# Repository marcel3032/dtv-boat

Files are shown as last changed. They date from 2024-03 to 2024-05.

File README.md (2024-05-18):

# dtv-boat

Zdrojáky a súbory k návrhu loďky na diaľkové ovládanie na predmet Digitálne technológie výroby.

## Úvod a popis lode

Cieľom projektu je postaviť diaľkovo ovládanú loďku.
Loďka bude z dreva (preglejka/balza), ktoré bude rezané na laseri.
Lodná skrutka, kormidlo a konzola kormidla bude tlačené na 3D tlačiarni.
Elektronická časť modelu sa skladá z 2,4GHz pištoľovej vysielačky a prijímača.
Pohon modelu sa skladá z jednosmerného (brushed) 21 závitového (21T) motora typu 550.
Regulátor je 80A na 2-3 článkovú LiXX alebo 4-9 článkovú Ni-XX baterku.
Regulátor má vstavaný 5A BEC, ktorý ale má 7.4V/6.4V.
~~Keďže prijímač a servo je do 6V, tak ho možno budeme musieť regulovať na menšie napätie,
čo zrejme budeme robiť výkonovou diódou.~~ Edit: servo aj prijímač 6.4V napájanie zvládnu, takže nakoniec takéto nebolo potrebné.
Ovládanie kormidla zabezpečuje 3kg servo, ktoré je dvojicou bowdenov spojené s kormidlom.

Chladenie motoru a regulátoru je vodné. Voda je odoberaná za lodnou skrutkou na kormidle, odkiaľ je tlakom hnaná cez regulátor a následne motor.
Pre motor sme kúpili medený vodný chladič, pre regulátor bol vyrobený z tenkej medenej/hliníkovej trubky vloženej medzi rebrovanie chladiča.

Výkon je z motoru vedený kardanovým kĺbom priamo na hriadeľ s lodnou skrutkou bez prevodovky alebo redukcie.
Hriadeľ je cez dvojicu ložísk osadená v puzdre, ktoré je vlepené do trupu lode.

## Lodná skrutka

Lodná skrutka je navrhnutá v programe OpenSCAD. [Zdrojový kód](propeller/propeller.scad) je v repozitári.
List lodnej skutky má elipsový tvar a je prehnutý (`skew`). List má po celej svojej dĺžky rovnaký profil, mení sa iba jeho hĺbka.
Profil listu je zo 4 číslnej NACA série, pre našu loď bol pôvodne vybratý profil NACA 2412, t.j. prehnutý profil s 12% hrúbkou.
List je samozrejme pre zachovanie koštantného stúpania počas celej dĺžky skrútený
( $\alpha = atan2(S, 2 \pi r)$ , kde $S$ je stúpanie listu a $r$ je vzdialenosť osi otáčania).

Zrejme budeme počas vývoja experimentovať s rôznymi priemermi, stúpaniami skutky a profilmi.

*Profil NACA 2412:*

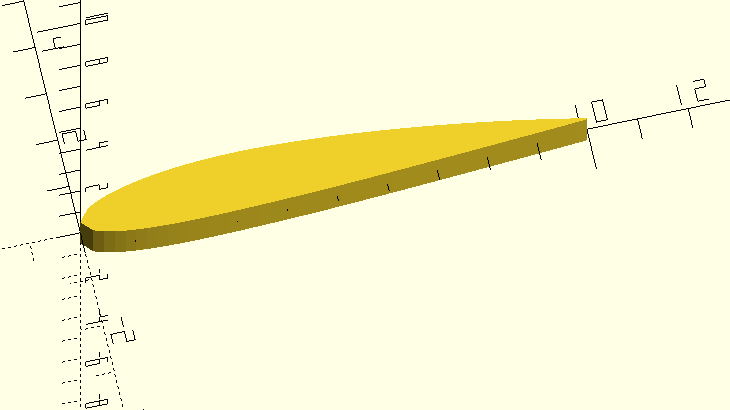
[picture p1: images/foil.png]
Profil NACA 2412


*Jeden list:*

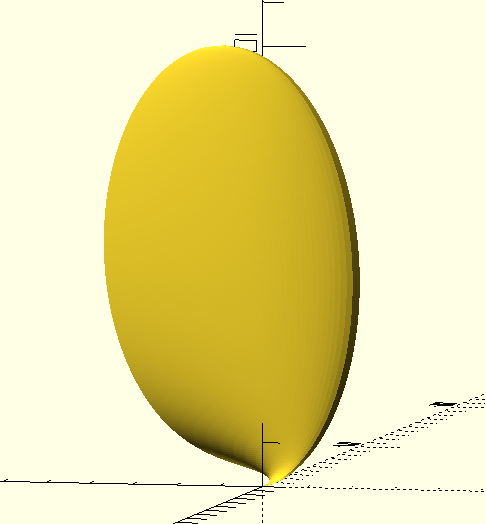
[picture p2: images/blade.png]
Jeden list


*Kompletná lodná skrutka aj s nábojom:*

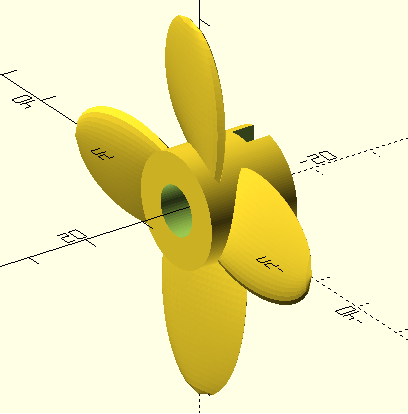
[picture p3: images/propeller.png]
Kompletná lodná skrutka aj s nábojom


## Trup lode

Trup lode je klasická drevená konštrukcia s preglejkovými priečkami a opláštením.
V trupe sa nachádzajú 4 priečne priečky (z toho posledné dve sú zdvojené) a 2 pozdĺžne.
Priečky rezané na laseri a sú z 3mm hrubej preglejky.

Opláštenie lode je z 1.5mm hrubej preglejky rezanej na laseri.

Trup lode je opäť navrhnutý v OpenSCADe a tvary priečok sú vyexportované priamo z tohoto programu.
[Zdrojový kód](boat.scad) je tiež v repozitári.

*Trup lode:*

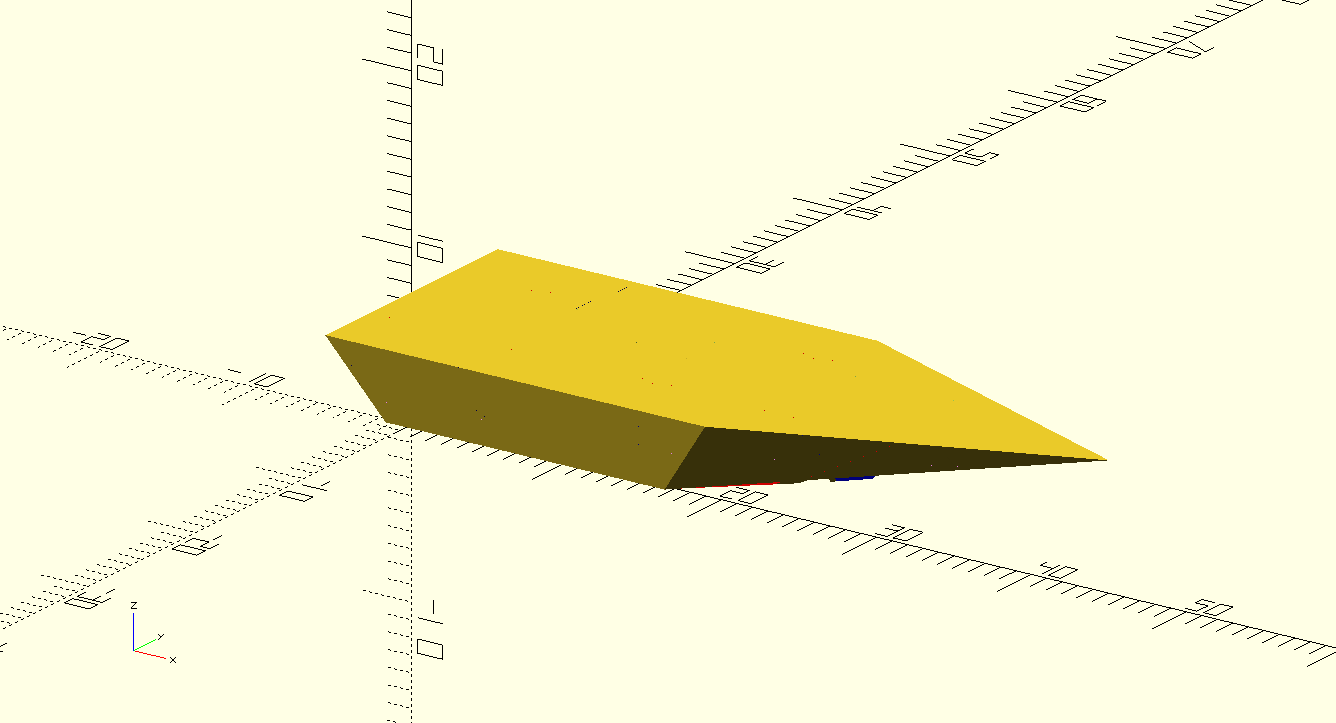
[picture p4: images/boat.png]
Trup lode


*Priečky v lodi:*

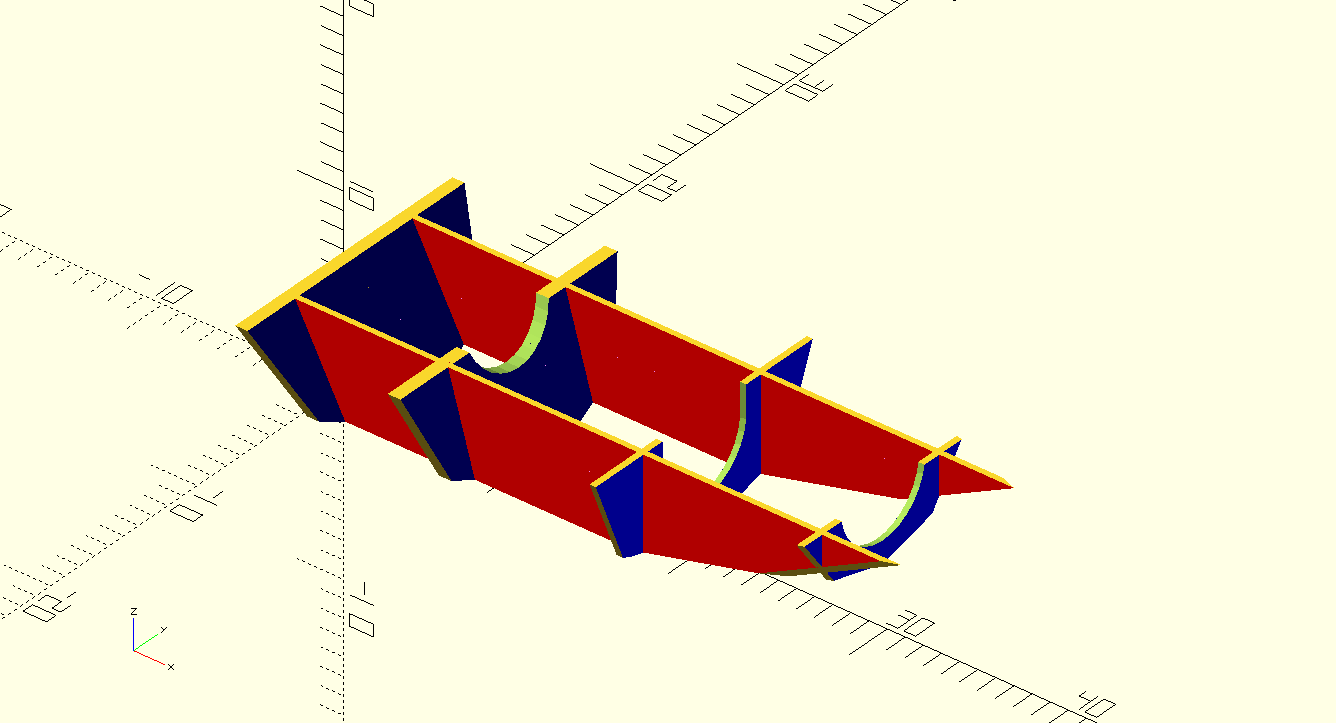
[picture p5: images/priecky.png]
Priečky v lodi


*Priečky pripravené na rezanie:*

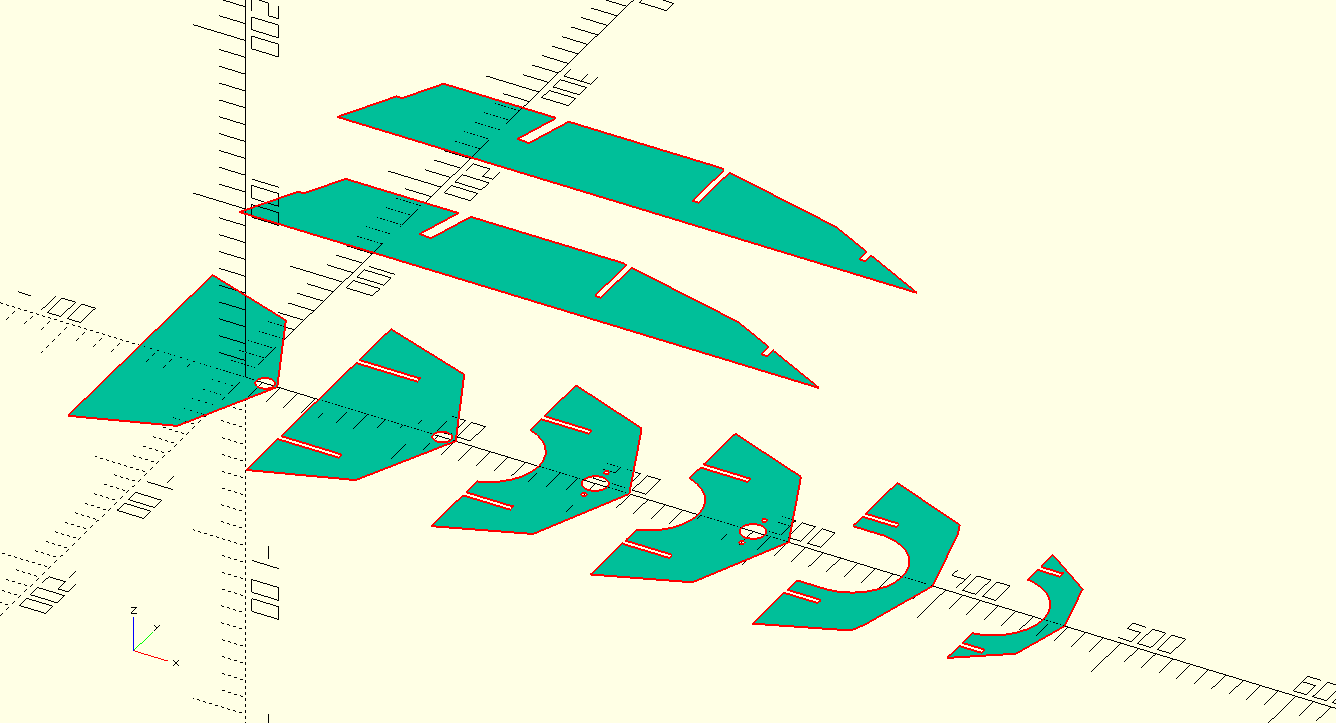
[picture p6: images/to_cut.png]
Priečky pripravené na rezanie


Opláštenie lode nie je priamo z OpenSCADu.
Namiesto toho sú z programu vyexportované súradnice vrcholov útvarov z ktorých sa opláštenie skladá.
Tieto útvary sú následne Python skriptom zrotované a sú vypočítané ich súradnice.
[Python skript](rotate_3d_polygons.py) je opäť v repozitári.

## Konzola kormidla a kormidlo

Konzola kormidla a kormmidlo boli navrhnuté v OpenSCADe a vytlačené na 3D tlačiarni.
Konzola má obdĺžnikový prierez a je k trupu lode cez plochú doštičku pripevnená štyrmi skrutkami M3.
Na konci konzoly je miesto na osku kormidla.
Oska je z nerezového drôtu priemeru 3.2mm a na vrchu je závlačkou pripevnená ku konzole.
Profil kormidla je rovnostranný trojuholník otočený základňou od smeru plavby.
Vo vnútri kormidla sa nachádza kanál na vstup chladiacej vody.
Vstup tohoto kanálu je otočený smerom k lodnej skrutke, aby tlačila vodu cez chladiaci kanál.
Z výstupu vodného kanála na vrchnej časti lode je voda odvádzaná umelohmotnou hadičkou ďalej do trupu lode.
Na vrchnej časti kormidla sa nachádzajú páky riadenia.

*Konzola kormidla aj s kormidlom (v zadnej časti kormidla je viditeľný kanál na chladiacu vodu):*

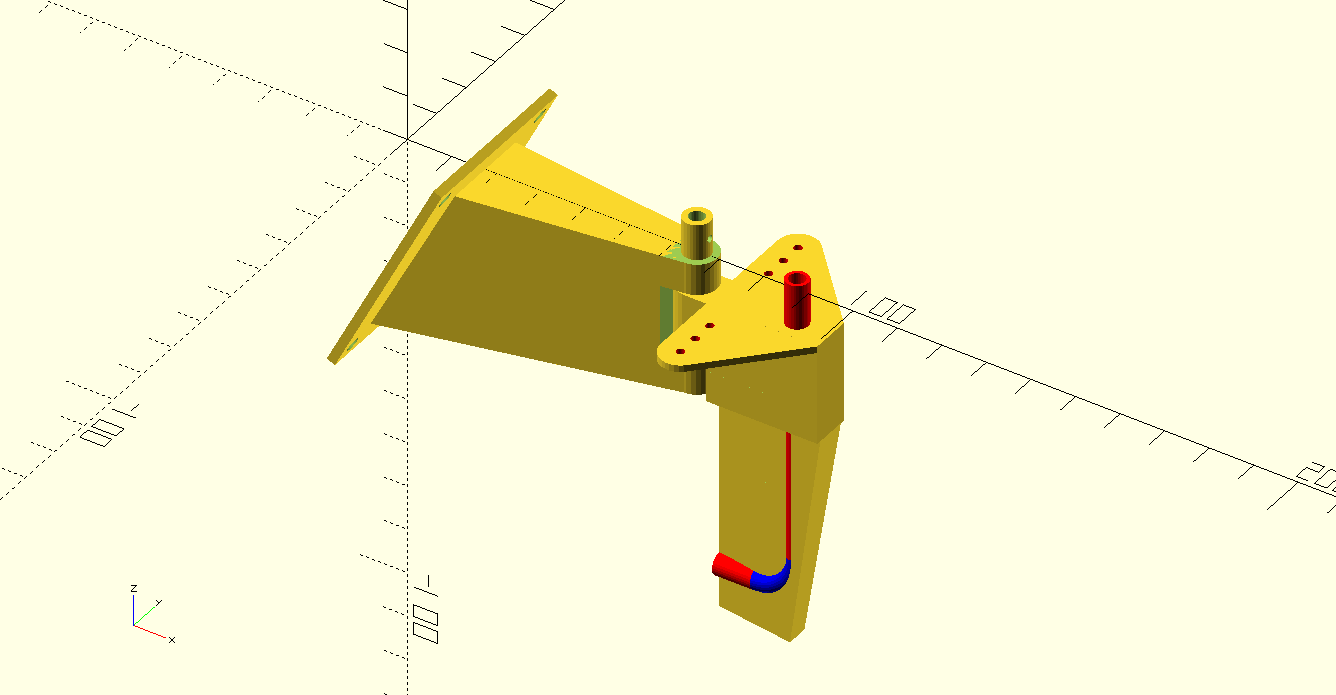
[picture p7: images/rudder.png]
Konzola kormidla aj s kormidlom (v zadnej časti kormidla je viditeľný kanál na chladiacu vodu)


## Stavba lode

Stavba lode začala narezaním potrebných dielov na laserovej rezačke.
Následne boli zlepené vnútorné priečky lode a vlepený hriadeľ a opláštenie lode.

*Vnútorné priečky:*

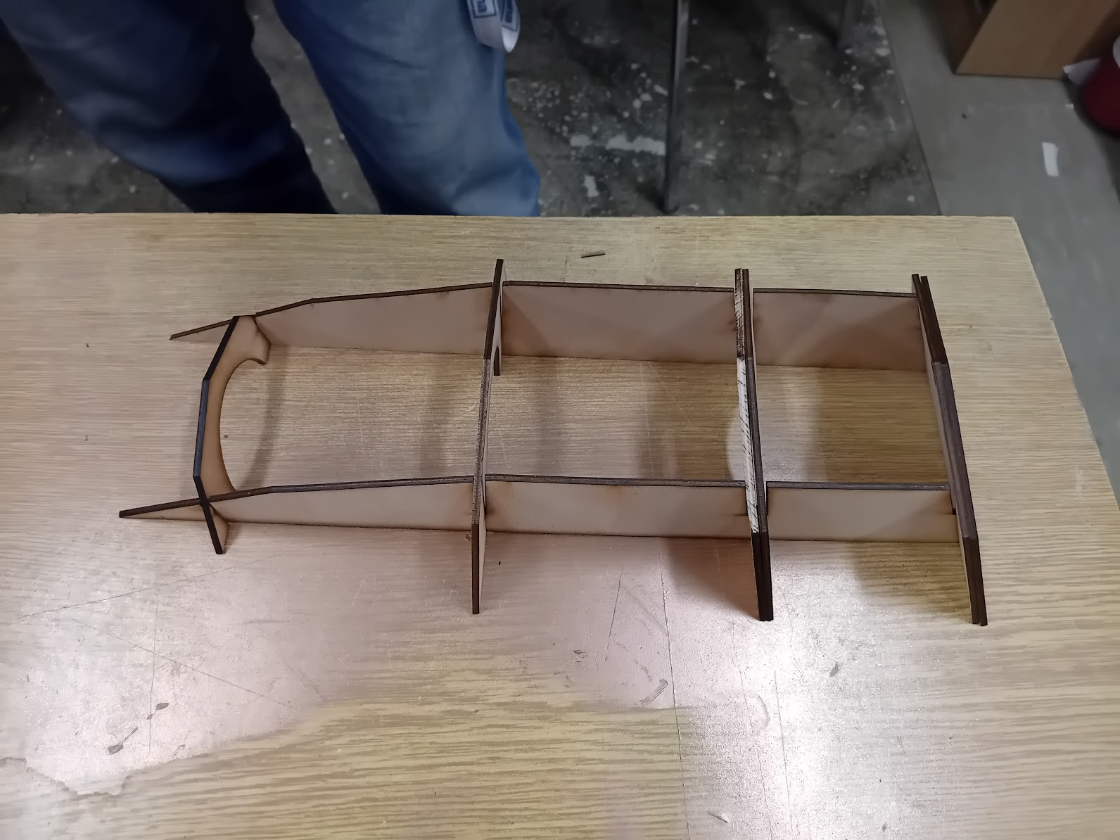
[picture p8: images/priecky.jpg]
Vnútorné priečky)


Do lode bol osadený motor a urobené lôžko na servo priečku.

*Detail kardanového kĺbu, motoru v silentblokoch a hranolčekoch pod servo priečku:*

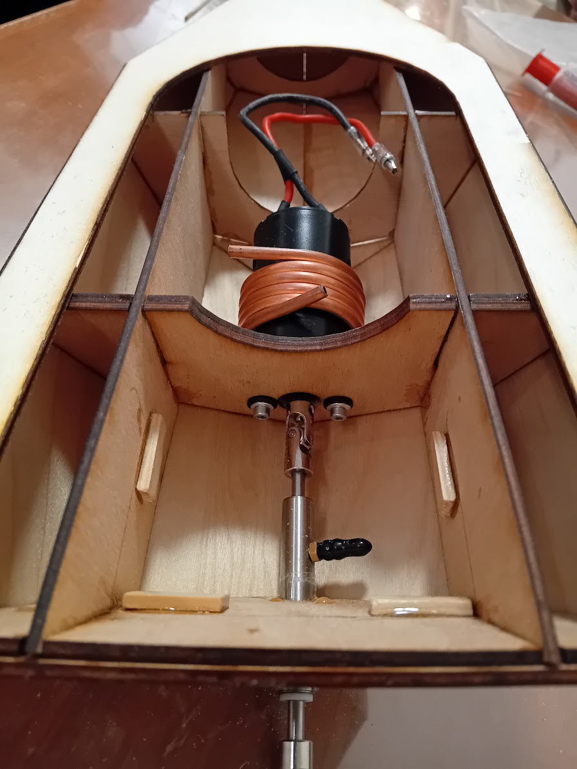
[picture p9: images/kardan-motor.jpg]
Detail kardanového kĺbu, motoru v silentblokoch a hranolčekoch pod servo priečku)


Stavba lode pokračovala prilepením horného opláštenia.
Týmto bola stavba drevenej konštrukcie lode hotová.

*Opláštená loďka:*

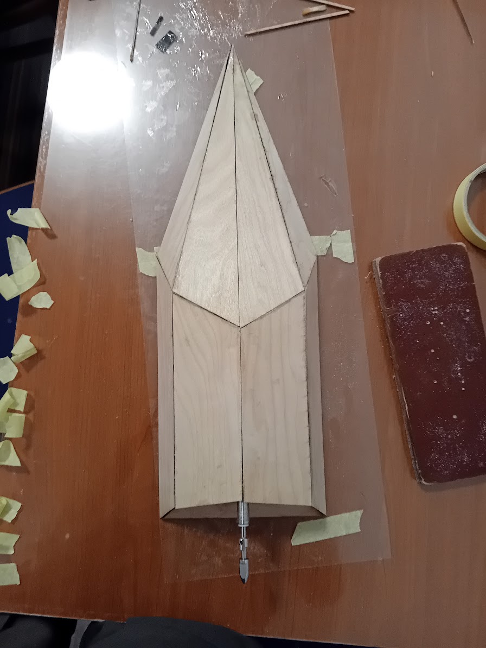
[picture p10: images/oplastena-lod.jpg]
Opláštená loďka)


Pokračovali sme olamimnovaním celého trupu lode dvomi vrstvami sklenej tkaniny gramáže $80 g/m^2$.
Laminovali sme epoxidovou živicou L285.

*Laminovanie:*

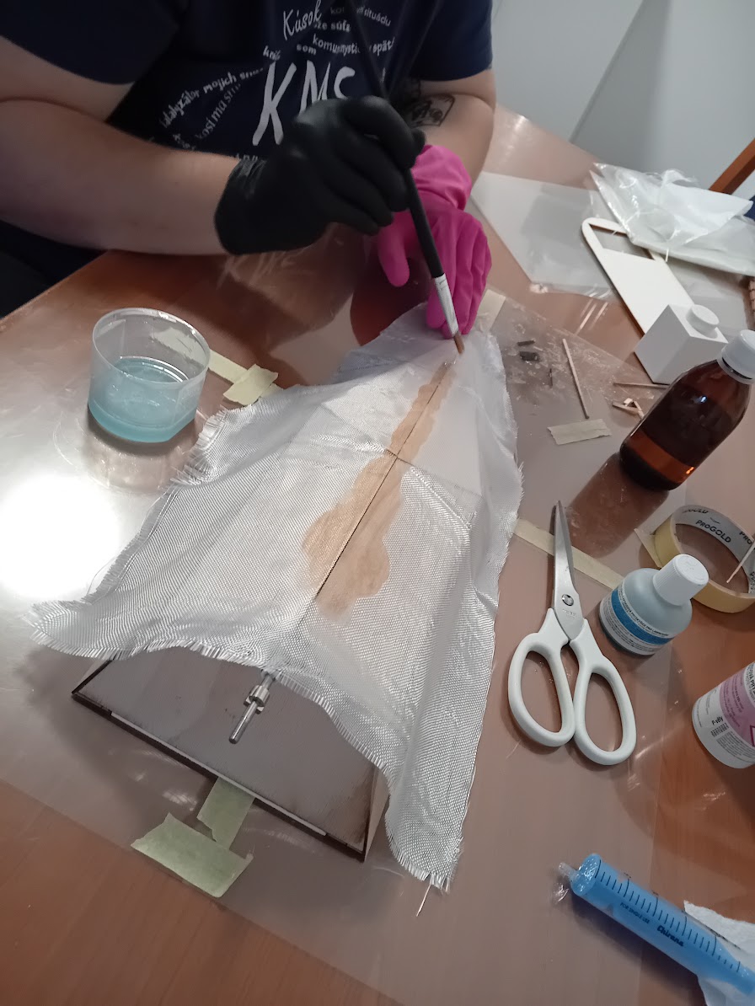
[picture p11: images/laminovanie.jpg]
Laminovanie)


Pri hranách, kde pod tkaninou vznikli bubliny sme ich odbrúsili a tieto miesta prelaminovali opäť.
Nasledovala povrchová úprava trupu.
Trup bol najprv vytmelený polyesterovým tmelom (gitom) a namokro prebrúsený.

*Vygitovaný trup:*

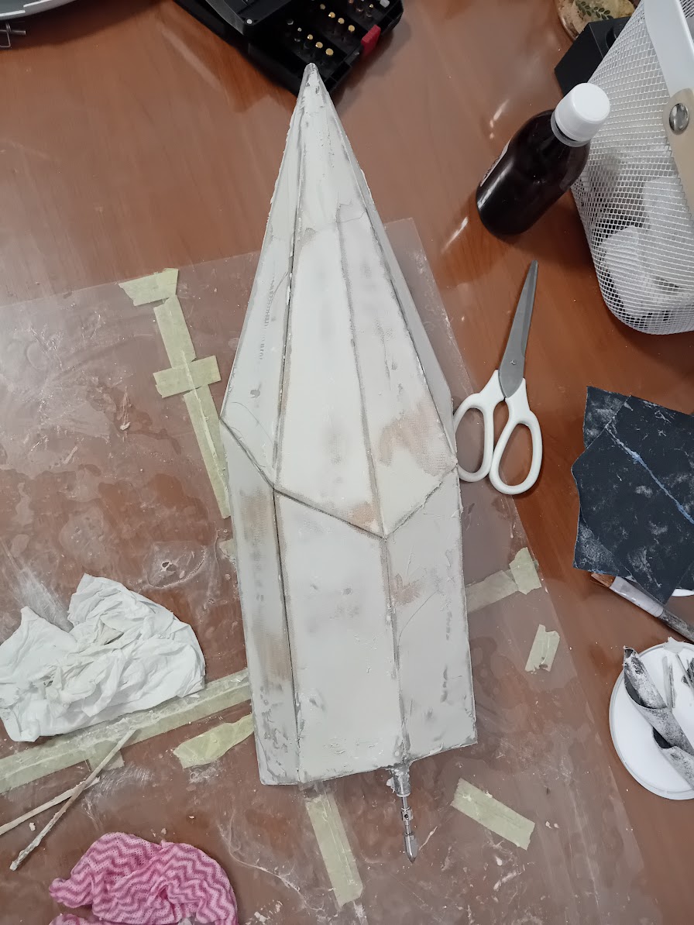
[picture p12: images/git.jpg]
Vygitovaný trup)


Následne bol trup nastriekaný plničom.

*Trup nastriekaný plničom:*

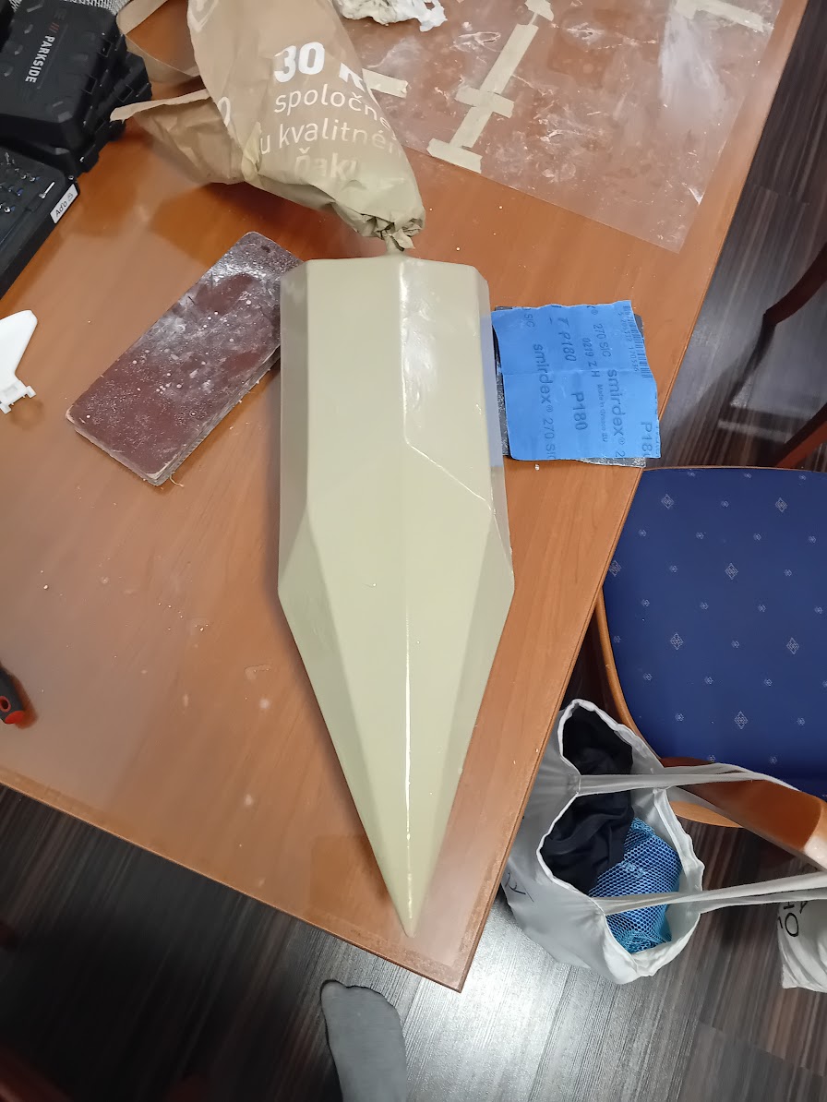
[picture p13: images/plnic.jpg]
Trup nastriekaný plničom)


Po finálnom mokrom prebrúsení bol trup nastriekaný vrchnou farbou.
Ako kamufláž bola zvolená bola modro-ružová farebná kombinácia (RAL 5002, RAL 4003).

*Kamufláž lode:*

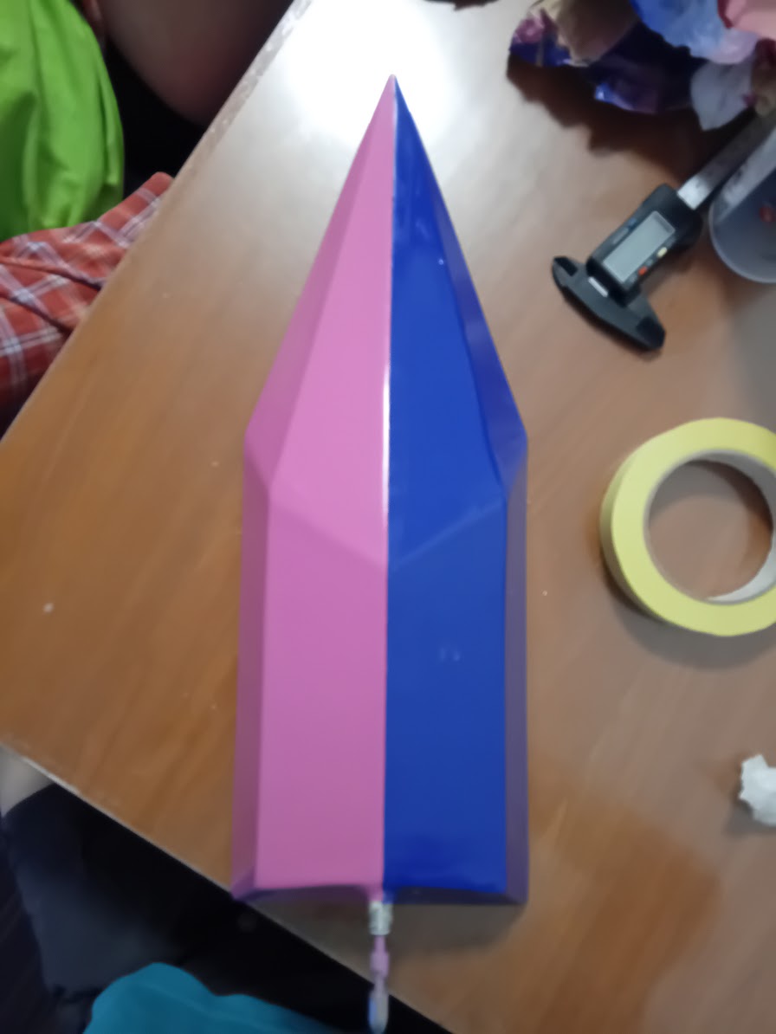
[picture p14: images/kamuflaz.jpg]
Kamufláž lode)


Paralelene s dokončovaním trupu prebiehal návrh a tlač kormidla a konzoly kormidla.
Boli tiež vytlačené vrchné kryty lode a lodná skrutka.

*Vytlačené kormidlo:*

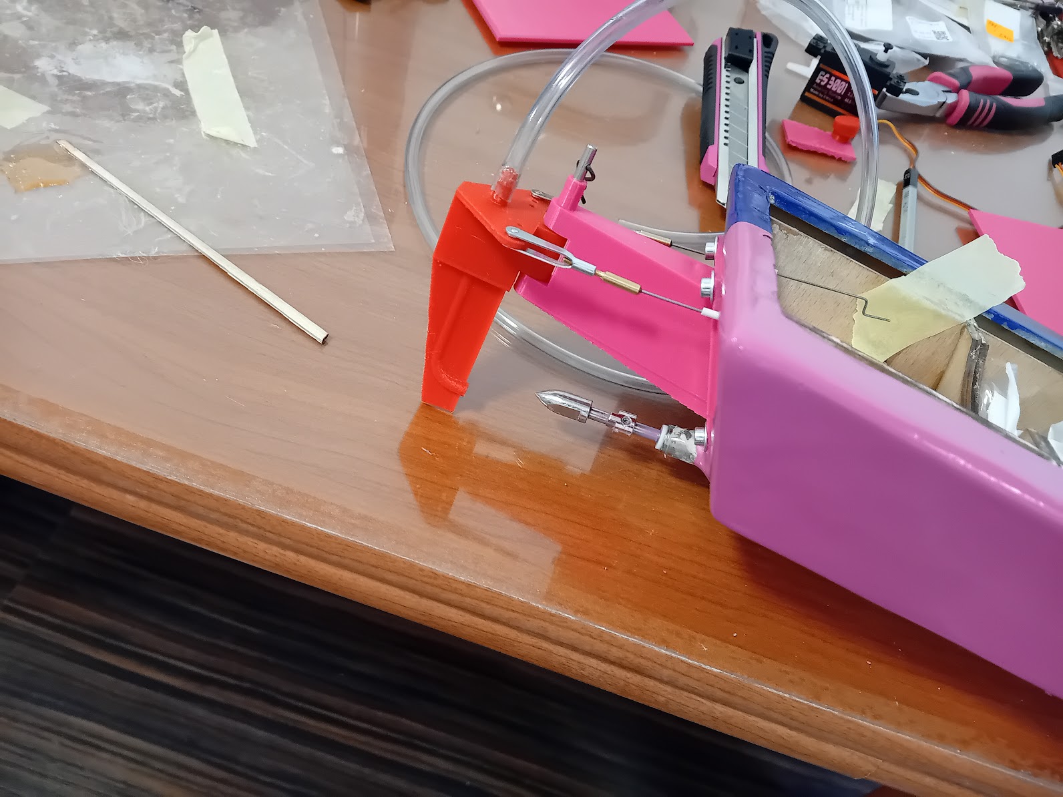
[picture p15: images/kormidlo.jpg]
Vytlačené kormidlo)


*Výsledná loďka bez jedného vrchného krytu:*

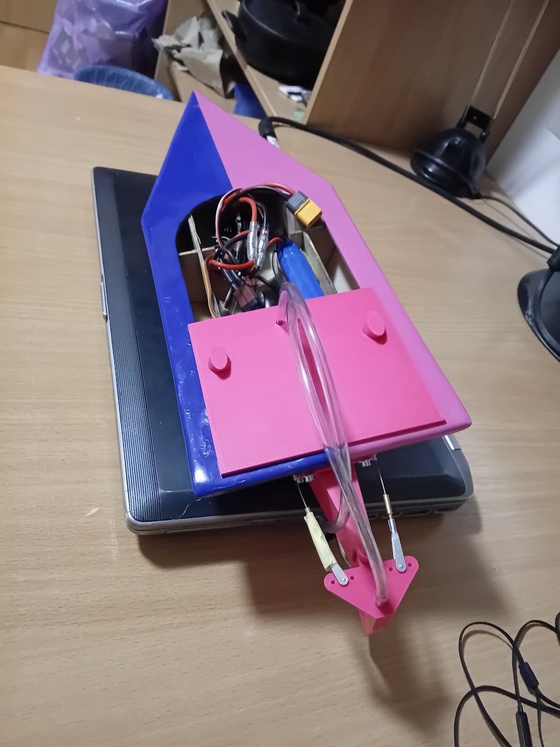
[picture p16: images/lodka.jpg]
Výsledná loďka bez jedného vrchného krytu)


## Testy lode a skúsenosti z používania

Loďka bola 15.5.2024 prvý krát vyskúšaná na vode, najprv vo vani a potom na Karloveskom ramene.
Vodné chladenie fungovalo bez problémov.
Kormidlo je dostatočne účinné a nevykazuje žiadne problémy s vôľami.
Loďka má pomerne veľký ponor, iba 1-2cm pod vrchnú hrany trupu.
Loďka je premotorovaná, takže s pôvodnou lodnou skrutkou priemeru 36mm (stúpanie neznáme, odhadom okolo 40mm)
nad tretinu plynu dochádza ku výraznej kavitácii, čo sa prejaví tvorbou veľkého množstva vzduchu za loďkou,
hrabaním skrutky vo vzduchu, zvýšeným hlukom a znížením rýchlosti loďky.

Z tohoto dôvodu bola na 3D tlačiarni vytlačená druhá skrutka s priemerom 40mm a stúpaním 48mm,
ktorá ale problém kavitácie neodstránila, ostal približne rovnaký.
Pri skúškach tejto lodnej skrutky sa prejavil ešte jeden problém:
cez bowdeny riadenia kormidla, popri tiahlach natiekla do loďky voda, vtiekla do serva,
kde vtiekla zrejme do potenciometra, ktorý sníma polohu výstupnej páky.
Je tiež možné, že voda zoskratovala niektoré častí elektroniky.
Následkom tohoto sa servo vychýlilo na jeden doraz (odpozorovaný jav)
a zrejme sa začalo mykať (toto sme bezprostredne na vode nevideli, ale počas skúšok serva na zemi sa prejavilo).
Týmto servo preťažilo BEC napájací obvod v regulátore na ktorom sa zapla ochrana proti preťaženiu
a servo prestalo byť napájané. Samozrejme, napájaný prestal byť aj prijímač, takže loďka prestala reagovať na ovládanie.
Nasledovalo plávanie za neovládanou loďkou.

### Zmeny oproti plánu

- Kvôli vode vtekajúcej do trupu cez bowdeny sme utesnili tiahla gumenými manžetami.
- Pôvodný plán bol zaisťovať vrchné kryty na trupe pomocou otočných poistiek ("camlockov"). Tieto poistky sa ale lámali a nemali žiadnu možnosť pritiahnutia krytov ku lodi, preto boli nahradené "klinmi".

### Odporúčania do budúcnosti

Loďka vyšla pomerne ťažká (takmer presných 1000g), čo sa prejavilo na jej veľkom ponore.
Riešenie je asi urobiť loďku o 10cm dlhšiu (55cm) pri zachovaní počtu vnútorných priečok.
Tiež je možné vnútorné priečky urobiť z tenšej preglejky (2mm by boli úplne dostatočné),
keďže aktuálne je loďka zbytočne pevná (aj opláštenie môže byť tenšie, pokojne 1mm).

Tiež mohol byť pre loď zvolený menší motor (540 by bolo úplne v poriadku), ktorý bude mať menšie otáčky.

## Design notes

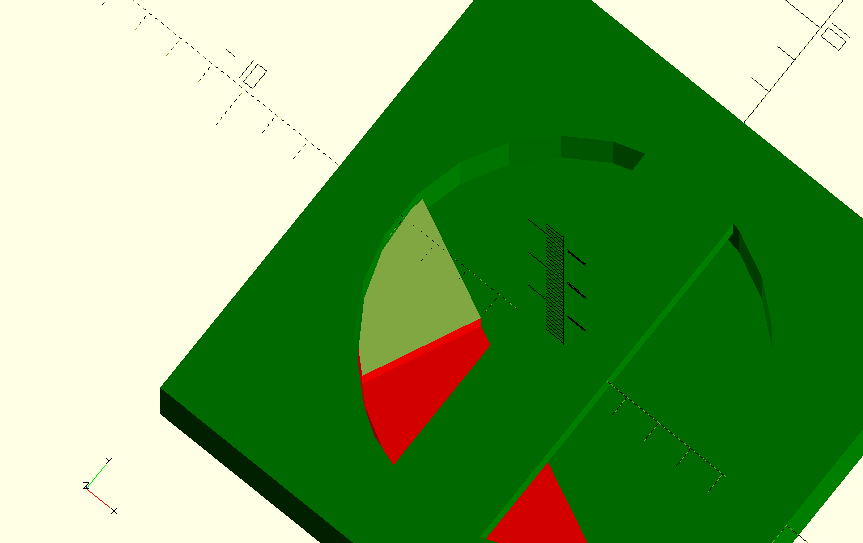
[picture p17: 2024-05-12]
images/camlock4.png

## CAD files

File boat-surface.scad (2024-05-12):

scale([10,10,10]){
    projection(){
        translate([0,5.5,0])
            polyhedron(points = [
            [ 3.75, 0.0, 0.0 ],
            [ 17.0, 0.0, 0.0 ],
            [ 20.5, 6.5, 1.3322676295501878e-15 ],
            [ 2.5, 6.5, 1.3322676295501878e-15 ]], faces=[[0,1,2,3]]);

        translate([0,4.5,0])
            polyhedron(points = [
            [ 24.11265131074969, 7.007418983796077, -9.485574624224707 ],
            [ 19.137244281156036, 2.507938470462337, -9.485574624224707 ],
            [ 44.61265131074969, -0.9925810162039239, -9.485574624224707 ]], faces=[[0,1,2]]);

        translate([5,0,0])
            polyhedron(points = [
            [ 45.41903201847357, 0.4073922401826391, -4.265625636118506 ],
            [ 20.27125292531581, 5.777607010723705, -4.265625636118509 ],
            [ 16.44736337873693, -0.5372856040057615, -4.265625636118509 ]], faces=[[0,1,2]]);

        translate([0,-5,0])
            polyhedron(points = [
            [ 24.5, 9.934700592472275, -4.642383454426296 ],
            [ 0.0, 9.934700592472275, -4.642383454426296 ],
            [ 2.5, 4.5495357853377705, -4.642383454426297 ],
            [ 20.5, 4.5495357853377705, -4.642383454426297 ]], faces=[[0,1,2,3]]); 
    }
}

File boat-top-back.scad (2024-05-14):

depth = 74;
boat_width = 110;
oversize = 7;
thickness = 2.8;
pipe_distance = 10;
pipe_d = 5.75;
screw_d = 3.5;
lock_side_offset = 5;
overisze_front = 30;

size = 4;
lock_width = 12;
lock_length = 5;

camlock_d=12;

big_eps = 0.5;

$fn=50;

//rotate([0,180,0])
translate([0,0,4])
back_cover_base();

module back_cover_base(){
    difference() {
        union(){
            translate([0,0,-thickness/2])cube([depth,boat_width,thickness],center=true);
            color("#a88132")translate([oversize/2,0,thickness/2])cube([depth+oversize,boat_width+2*oversize,thickness],center=true);
            color("green")translate([-depth/2-overisze_front,-boat_width/2-oversize,0])cube([overisze_front,boat_width+2*oversize,thickness]);
            color("blue")translate([-depth/2-2/3*overisze_front,-30/2,-thickness])cube([2/3*overisze_front,30,thickness]);
        }
        translate([-depth/2-15,+pipe_distance/2,0]) rotate([0,0,0]) cylinder(h=thickness*10,d=pipe_d, center=true);
        translate([-depth/2-15,-pipe_distance/2,0]) rotate([0,0,0]) cylinder(h=thickness*10,d=pipe_d, center=true);
        
        translate([-depth/2+8,+(boat_width/2-camlock_d/2-1),0]) rotate([0,0,0]) cylinder(h=thickness*10,d=camlock_d, center=true);
        translate([-depth/2+8,-(boat_width/2-camlock_d/2-1),0]) rotate([0,0,0]) cylinder(h=thickness*10,d=camlock_d, center=true);
        /*
        translate([0,-boat_width/2+lock_side_offset,-thickness-size/2])
            color("red")lock_hole();
        translate([0,-(-boat_width/2+lock_side_offset),-thickness-size/2])
            lock_hole();
        */
    }
}

/*
module lock(){
        translate([0,lock_length+size,0]) rotate([0,90,0])
                cylinder(h=lock_width+size, d=size-big_eps, center=true);
        length = lock_length+lock_side_offset+10;
        translate([0,-length/2+lock_length+size,0])
            difference() {
                cube([lock_width-size-big_eps, length, size-big_eps], center=true);
                translate([0,-length/2-size+1,-size]) rotate([20,0,0])
                        cube(10, center=true);
                lock_hole();
            }
}

module lock_hole(){
        cylinder(h=thickness*10,d=screw_d, center=true);
}

module lock_holder(){
        translate([lock_width/2,lock_length,0])cube(size, center=true);
        translate([-lock_width/2,lock_length,0])cube(size, center=true);
        translate([0,2*size+lock_length,0])cube([lock_width+size,size,size], center=true);
}
*/

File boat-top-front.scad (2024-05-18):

depth = 74;
boat_width = 110;
oversize = 7;
thickness = 2.8;
big_eps = 0.5;

$fn=25;

d = 12;

cube_d = 24.5-7.45-d/2;

translate([0,0,--(thickness+1)]){
    //top_front();
    translate([80,0,1])rotate([0,0,180])shield();
}

module shield(){
    difference(){
        linear_extrude(25, convexity=20, scale=[0.45,0.8])
            outline();
        translate([30,-60,-50]) rotate([0,-15,0]) cube([50,120,100]);
    }
}

module outline(){
    {
        difference(){
            polovica();
            translate([0.1,0,0])scale([0.9,0.97,1])polovica();
        }
    }
}


module polovica(){
    dlzka = 30;
    sirka = 30;
    hull(){
        translate([-dlzka,sirka,0])circle(20);
        translate([-dlzka,-sirka,0])circle(20);
        translate([dlzka,sirka,0])circle(20);
        translate([dlzka,-sirka,0])circle(20);
    }
}

module top_front(){
    translate([0,0,-thickness])linear_extrude(thickness) 2d_front();
    oversized_top();
    difference(){
        translate([-14,0,-thickness/2])cube([28,110,thickness], center=true);
        scale([1.01, 1.01, 1.1])translate([-20/2-10,0,-thickness/2+0.1])cube([22,32,thickness], center=true);
    }
}

module oversized_top(){
    translate([0,0,-0.01])linear_extrude(thickness) scale([(175+oversize)/175, (boat_width+2*oversize)/boat_width, 1]) 2d_front();
}

module 2d_front(){
    projection() 
    scale([9.9,9.165,10]){
        translate([-20+cube_d,0,-1]){
            union(){
                translate([20,0,0])cylinder(20,d=d);
                translate([-cube_d/2+20,0,0])cube([cube_d,d,30], center=true);
            }
        }
    }
}

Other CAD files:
boat.scad
camlock.scad
old-boat-top-front.scad
outline.scad
propeller/blade.scad
propeller/naca-foil.scad
propeller/propeller-linear-twist-and-scale.scad
propeller/propeller.scad
rudder.scad

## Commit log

2024-03-16 add propeler `.scad` files
    [blade.scad, naca-foil.scad, propeller-linear-twist-and-scale.scad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]
2024-03-17 add boat fuselage
    [boat.scad]
2024-03-17 render ready to cut priecky
    [boat.scad]
2024-03-18 small tweaks in boat.scad
    [boat.scad]
2024-03-30 update propeller.scad, boat fuselage tweaks, add boat surface panels
    [boat-surface.scad, boat.scad, propeller.scad]
2024-03-30 fix hriadel hole
    [boat.scad]
2024-05-12 many updates
    [boat-surface.scad, boat-top-back.scad, boat.scad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]
2024-05-14 add rudder
    [rudder.scad]
2024-05-14 add boat top, some updates
    [boat-top-back.scad, boat-top-front.scad, boat.scad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]
2024-05-16 lenght -> length
    [rudder.scad]
2024-05-18 various updates, add up-to-date images
    [boat-top-front.scad, boat.scad, camlock.scad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]
2024-05-18 update readme, add photos
    [rudder.scad]
